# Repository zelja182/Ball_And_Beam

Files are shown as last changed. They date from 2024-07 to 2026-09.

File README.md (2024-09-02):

Sistem za balansiranje lopte na šini

Ovaj projekat se bavi problemom balansiranja lopte na šini i za potrebe istog je uređeno sledeće:
- Isporjektovan sistem za balansiranje lopte na šini u programu za CAD dizajn
- Svi isporjektovani delovi su izštampani na 3D štampaču
- Određen je matematički model sistema
  - Odeđena je jednačina kretanja lopte po šini
  - Određen matematički model hobi servo motora uz pomoć metoda za identifikaciju sistema, odnosno to pokriva
    - Projektovanje platforme za ispitivanje u programu za CAD modeliranje
    - Pokretanje ekspirimenata, prikupljnje i obradu podataka
    - Grey box metod identifikacije sistema - gde je na osnovu poznatih informacija formirana prenosna funkcija, a zatim vrednosti parametra te prenosne funkcije na osnovu prikupljenih i obrađeninih podataka i funkcijom minimizacije estimirani
    - Black box metod identifikacije sistema - cilj ovog dela jeste određivanje matematičkog modela uz pomoć neuronskih mreža i atoregresivnog modela. Preuzeto iz rada https://www.sciencedirect.com/science/article/pii/S2405896320317353
- Konstruisanje i implementacija upravljačkog sistema  --> in progress
- Upoređivanje rezultata simuliranog i stvarnog sistema  --> in progress

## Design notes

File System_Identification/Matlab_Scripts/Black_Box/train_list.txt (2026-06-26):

../../Data/Encoder_data/Test_2/Test_30/Processed/Test_1.csv
../../Data/Encoder_data/Test_2/Test_30/Processed/Test_2.csv
../../Data/Encoder_data/Test_2/Test_30/Processed/Test_4.csv
../../Data/Encoder_data/Test_2/Test_30/Processed/Test_5.csv
../../Data/Encoder_data/Test_2/Test_30/Processed/Test_6.csv
../../Data/Encoder_data/Test_2/Test_30/Processed/Test_9.csv
../../Data/Encoder_data/Test_2/Test_30/Processed/Test_10.csv
../../Data/Encoder_data/Test_2/Test_30/Processed/Test_11.csv
../../Data/Encoder_data/Test_2/Test_30/Processed/Test_12.csv
../../Data/Encoder_data/Test_2/Test_30/Processed/Test_13.csv
../../Data/Encoder_data/Test_2/Test_30/Processed/Test_14.csv
../../Data/Encoder_data/Test_2/Test_45/Processed/Test_1.csv
../../Data/Encoder_data/Test_2/Test_45/Processed/Test_2.csv
../../Data/Encoder_data/Test_2/Test_45/Processed/Test_3.csv
../../Data/Encoder_data/Test_2/Test_45/Processed/Test_4.csv
../../Data/Encoder_data/Test_2/Test_45/Processed/Test_5.csv
../../Data/Encoder_data/Test_2/Test_45/Processed/Test_7.csv
../../Data/Encoder_data/Test_2/Test_45/Processed/Test_8.csv
../../Data/Encoder_data/Test_2/Test_45/Processed/Test_10.csv
../../Data/Encoder_data/Test_2/Test_45/Processed/Test_12.csv
../../Data/Encoder_data/Test_2/Test_45/Processed/Test_13.csv
../../Data/Encoder_data/Test_2/Test_45/Processed/Test_14.csv

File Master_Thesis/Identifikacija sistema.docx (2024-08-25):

# Identifikacija Sistema

Ovde je cilj da se opise ceo postupak identifikacije sistema

# Black Box vs Grey Box method

Ovde hocu da predstavim kako ova dva modela rade i njihove generalne ideje

# Eksperimentalno odredjivanje prenosne funkcije dc servo motora

Ovde hocu da opisem ceo postupak odredjivanje prenosne funkcije

## Prikupljane i obrada podataka

## Grey Box method i Validacija istog

### Matematicki model servo motora

Ovde hocu da objasnim kako sam nasao generalnu prenosno f-ju servo motora

### Grey box metod i validacija

Ovde hocu da opisem kod koji sam koristio za estimaciju i validaciju prenosne f-je

## Black Box method i validacija istog

### Neuralne mreze kao alat u automatskom upravljanju

Kratak uvod u kojem hocu da spomenem DL i objasnim kako se on koristi u automatskom upravljanju --> Akcenat na identifikaciju sistema

### Black Box method

Ovde hocu da opisem kod koji sam koristo za estimaciju i validaciju prenosne funkcije

Izvori:

- Servo Motor tf identification:
  - https://faculty-web.msoe.edu/meier/ee3720/technotes/dcservo.pdf
- System identification:
  - https://indico.cern.ch/event/11749/contributions/1328397/attachments/57048/82143/control_theory_3.pdf
  - https://www.mathworks.com/help/ident/gs/about-system-identification.html
  - https://underactuated.mit.edu/Spring2022/
  - http://groups.csail.mit.edu/locomotion/russt.html
  - https://www.youtube.com/watch?v=YiJRgKJ0My8
  - https://www.youtube.com/watch?v=Z1QS6FsxrJI

Математички модел система

У уводу овог рада смо објаснили укратко конфигурацију систиама, а онда у поглављу “Пројектовање и израда система” објаснили како смо тај систем испројектовали у софтверу за компјутерски адитивни дизајн и затим уз помоћ 3D штампача израдили испројетоване делов које смо касније склопили.

Већ је познато да се наш систем састоји од лоптице која се креће по шини која је спрегнута са серво мотором преко полуга различитх дужина. Да ће нам

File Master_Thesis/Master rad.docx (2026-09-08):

# Мастер рад

# 1. Увод

Управљање нестабилних система је веома важан задатак у аутоматском управљању, а како се ови системи сматрају веома опасним они се испитују у лабораторијама. Систем за балансирање кугле на шини јесте нестабилан систем и може се поистоветити са реалним проблемима као што су хоризонтална стабилизација авиона током слетања или у средини турбулентног струјања.

Систем за балансирања кугле на шини је веома лак за разумевање и многе технике управљања се могу изучавати на њему, па се због тога често може наћи у лабораторијама инжeњера за аутоматско управљање.

Овај систем се састоји од кугле и шине чији се угао заокретања управља мотором. Циљ оваквог система јесте да се кугла заустави на тачно одређеној позицији. Ако је управљање лоше, кугла ће пасти са шине.

Систем балансирања кугле на шини може се реализовати у две конфигурације.

Прва конфигурација је приказана на слици 1.1. Са слике се види да је греда ослоњена у средини и да се ротира око своје централне осе. Оваква конфигурација поседује две предности. Прва предност је та што је лака за израду, а друга јесте то што јој је математички модел релативно једноставан.

Слика 1.1 – Конфигурација 1

Друга конфигурација је нешто сложенија, а приказана је на слици 1.2. У овој конфигурацији греда има две тачке ослонца. Један крај је непокретан и греда се ротира око његове тачке, док је други крај преко система полуга спојен на мотор. Оваква конфигурација је тежа за израду и има мало сложенији математички модел.

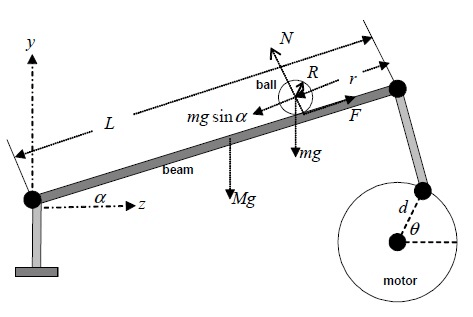
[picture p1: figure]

Слика 1.2 – Конфигурација 2

У овом раду се користи друга конфигурација, упркос сложености. Такође, треба напоменути да су следеће теме обрађене:

- Пројектовање и изрaда система за балансирање кугле на шини,
- Одређивање математичког модела система за балансирање кугле на шини,
- Пројектовање и имплементација регулатора и
- Испитивање у реалном времену.

# 2. Пројектовање и израда система за балансирање кугле на шини

Први проблеми и задаци овог мастер рада јесу пројектовање и израда система за балансирање кугле на шини. А да би се уопште могло испројектовати систем за балансирање кугле на шини потребно је знати одговоре на питања “Шта је циљ овог система? И како уопште он ради?”.

Циљ овог система јесте да доведе куглу на одређену позицију тако што ће сам себе избацити из равнотежног стања. Да би се то боље разумело, претпоставимо да имамо шину дугачку 50cm, да се кугла налази и мирује на десном крају те шине и да је жељена позиција те исте кугле средина шине. У следећем кораку, на основу жељене вредности излаза, мотор треба да заротира излазно вратило за угао α и нагне шину на лево, односно за угао β, сензор очита нову позицију кугле, која сада креће према средини, а затим регулатор на основу разлике жељене и стварне позиције кугле формира нови управљачки сигнал за мотор. У другом кораку мотор ће поново заротирати излазно вратило за угао α и кориговаће угао шине, а сензор очита нову позицију кугле и помоћу регулатора формирати нови сигнал за мотор. Ови кораци ће се понављати све док се кугла не доведе на жељену позицију. Све претходно објашњено може се представити и једним блок дијаграмом који је приказан на слици 2.1.

Слика 2.1 – Уопштени блок дијаграм система за балансирање кугле на шини

На основу блок дијаграма и изабране конфигурације система могу се формирати и додатна потпитања:

- Којим сензором се мери позиција кугле на шини? Којим мотором се гони цео систем? Којим контролером се систем управља?
  - За мерење позиције изабран је ласерски сензор удаљености VL53L0X, за извршни орган серво мотор непознатог произвођача и за формирање и прослеђивање управљачког сигнала микроконтролер Arduino Uno. Техничка документација и више информација о овим компонента, као и осталим компонентама које су коришћене приликом израде овог мастер рада, може се пронаћи на крају овог рада у додатку А.
- Како ће се сви испројектовани, нестандардни, делови израдити?
  - Сви делови који су испројектовани за овај мастер рад су израђени адитивном технологијом израде, тј. на 3D штампачу.

## 2.1. Пројектовање система за балансирање кугле на шини

Након што су дати одговори на сва претходна питања, слика самог система постаје јаснија и може се приступи пројектовању и моделирању система.

Први део који је испројектован јесте шина и она је кроз пар итерација добила следећи облик:

Слика 2.2 – Шина са куглом

Са слике се може видети да се шина састоји од четири дела: две половине шине и два граничника. Половине шине су међусобно спојене вијчаном везом на средини, док су граничници причвршћени епоксидним лепком на њеним крајевима.

Једна половина шине поседује ушицу која служи за спајање са ослонцем. На њеном крају налази се и граничник са ушицом, преко које се шина, посредством система полуга, повезује са мотором. Други граничник уједно представља носач ласерског сензора удаљености.

Следећи испројектовани део јесте носач шине. Носач се састоји из три дела; ушице, навојне шипке и базе. Делови су спојени навијањем на навојну шипку. На једном крају шипке навијена је ушица, а на другом база. Цео носач је затим зашрафљен за постоље од иверице.

Слика 2.3 – Шина са носачем

Након шине и носача, било је потребно испројектовати и додати везу између шине и мотора, сензор, микроконтролер и носаче за микроконтролер и серво мотор. Веза између шине и мотора се састоји из две полуге различитих дужина, где је дужа полуга повезана са шином на једном крају, а на другом крају са мањом полугом, која је повезана са серво мотором.

Финални модел система за балансирање кугле на шини приказан је на слици 2.4

Цео овај систем је измоделиран у софтверу за Компјутерски Адитивни Дизајн (CAD) CATIA и може се пронаћи на следећем линку:

https://github.com/zelja182/Ball_And_Beam/tree/main/Ball_and_Beam_CAD_model

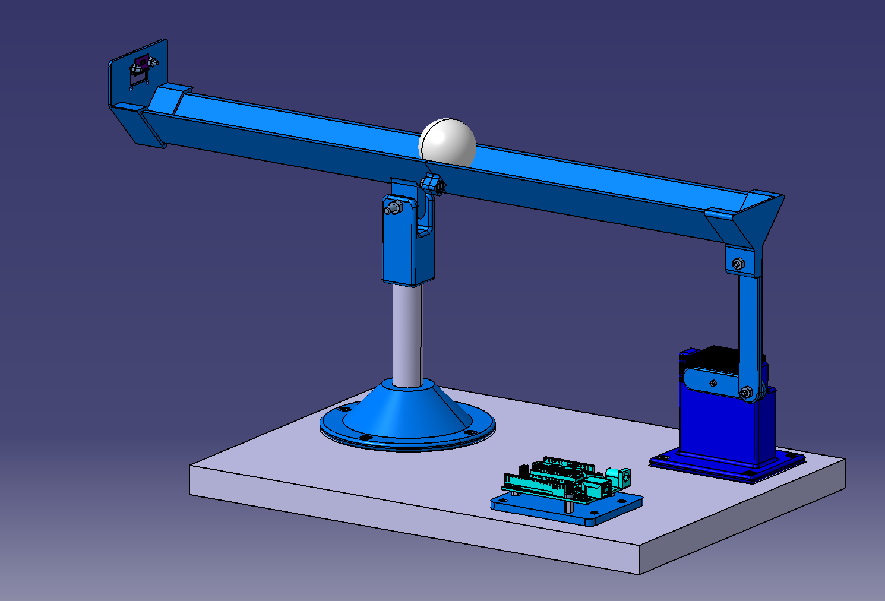
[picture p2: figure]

Слика 2.4 – Систем за балансирање кугле на шини

## 2.2. Израда пројектованих делова

Адитивна производња, позната и као 3D штампа или адитивна израда, је процес израде тродимензионалних објеката додавањем материјала у слојевима, уместо сечења или обликовања материјала.

У адитивној производњи, машине користе податке о CAD моделу да би додавале материјал у слојевима да би се израдио објекат, за разлику од традиционалних начина производње где машине уклањају материјал из блока или компоненте да би се добио жељени део.

Адитивна производња, у даљем тексту 3D штампа, има многе предности у односу на традиционалну производњу, укључујући већу сложеност дизајна, брзину производње, ниског трошкова производње малих серија или јединичних производа, могућност производње на захтев и низ других предности.

Због свих ових предности 3D штампач је нашао велику примену у различитим индустријама као што су авио и аутомобилска, медицинска и многе друге индустрије, али поред индустрије 3D штампач је постао и стандардна опрема многих лабараторија, као и радионица разних хобиста.

Постоје различите врсте 3D штампања, а неке од њих јесу фузија ласера, слој по слој (FDM) и селективна ласерска синтеризација (SLS). Која ће се врста 3D штампе користити зависи од жељеног материјала, величине објекта и других фактора.

За потребе мастер рада, сви пројектовани, нестандардни, делови израђен су на 3D штампачу Ender 3 Pro (слика 2.5) компаније Creality. Овај штампач користи технологију слој по слој (FDM), а његове основне карактеристике могу се видети у табели 2.1.

Слика 2.5 – Ender 3 Pro

Назив штампача | Ender 3 Pro
Запремина штампања | 220x220x250mm
Габарити штампача | 440x410x465mm
Пречник млазнице | 0.4mm
Максимална температура млазнице | 250°C
Максимална температура подлоге за штампање | 110°C
Висина слоја | 0,1–0,4mm
Повезвање | USB, SD картица
Материјали за штампање | PLA, ABS, PETG, TPU

Техничке карактеристике штампача Ender 3 Pro – Табела 2.1

Припрема делова за штампу је урађена у софтверу UltiMaker Cura. Сви делови су израђени од PLA пластике и са истом прецизношћу и за ту потребу температура подлоге за штампу је подешена на 55°C, температура млазнице на 215° и висина слоја на 0,2mm. Параметри попут дебљине зида, типа и густине испуне разликују се од дела до дела.

За израду свих делова, узимајући у обзир и шкартове, било је потребно 96 сати. Систем је склопљен следећим редом:

1. Састављање носача шине
2. Састављање шине и монтирање сензора на исту
3. Позиционирање и фиксирање носача шине и носача серво мотора
4. Спајање шине и носача шине
5. Монтирање серво мотора на носач истог
6. Спајање шине и серво мотора полугом
7. Позиционирање и фиксирање носача за микро контролер
8. Монтирање микроконтролера на носач за исти
9. Ожичавање система пратећи шему са слике 2.6

Слика 2.6 – Шема повезивања система за балансирање кугле на шини

# 3. Математички модел система за балансирање кугле на шини

Аутоматско управљање је мултидисциплинарна грана инжењерства усмерена на пројектовање, анализу и имплементацију система који контролишу понашање динамичких процеса. Главни задаци ове гране јесу идентификација система, која обухвата моделирање система, процену параметара и валидацију модела, и управљање системом, чији је циљ да систем учини стабилнијим, одзивнијим и прецизнијим.

На основу претходно реченог лако је закључити да су наредна два корака идентификација система и пројектовање алгоритма за управљање. С обзиром да је познавање математичког модела система предуслов за пројектовање алгоритма за управљање, онда је и јасно да ће у овом поглављу главни циљ бити идентификација самог система, односно одређивање његовог математичког модела.

Дефиниција 1 Модел физичког система је идеализовани, замишљени, систем који задржава особине стварног система битне за његову анализу.

Дефиниција 2 Математички модел система је формални математички опис модела физичког система који успоставља једнозначну везу између излазних и улазних величина за произвољне промене улазних величина и за произвољне почетне услове, а исказан је помоћу математичких симбола, операција и релација.

Ако се претпостави да математички модел довољно тачно описује физички систем, тј. модел физичког система, и да представља његов веродостојан опис, онда он садржи све информације о физичким особинама система. Тада се проучавање тог физичког система могу извршити на његовом математичком моделу.

У колико су динамика система и његови параметри познати, до математичког модела система може се доћи користећи законе физике. Претпоставимо да је систем представљен на следећој слици:

Слика 3.1 – Систем пригушеног осцилаторног кретања тела

и да су познати сви параметри овог система C, k и m. Користећи знање Механике може се закључити да овај систем преставља пригушено осцилаторно кретање тела и да се он може описати следећом једначином:

m (d^2 y)/(dt^2)+c (dy)/(dt)+ky(t)= F(t) (3.1)

Претходна једначина јесте математички модел система са слике која се даље може користити за анализу система. Овакав систем се у жаргону назва белом кутијом, јер су сви његови параметри познати, као и његова динамика.

Супротно од беле кутије, јесте црна кутија, односно модели чија динамика је непозната. У оваквим случајевима идентификација система, као засебна област аутоматског управљања, долази до изражаја.

Приликом одређивања математичког модела система непознате динамике, први корак јесте прикупљање информација о систему. Овај корак подразумева извођење експеримената над системом и то тако што се систем побуђује одређеним улазним величинама, а сам излаз система мери.

Следећи корак би био одабир структуре модела. За структуру система може се одабрати преносна функција са n-тим бројем полова и m-тим бројем нула, диференцијална једначина, ауто-регресивни модел, неуронска мрежа или било који други модел.

Након што су прикупљене информације о систему и одабрана структура модела, потребно је естимирати параметре и валидирати модел. Приликом валидације система треба користити нов сет података, где ће се улази тог сета искористити за побуду модела, а затим излази модела и стварног система поредити.

Када се све сумира, идентификација система се састоји од експеримента и прикупљање улазно-излазних података система, одабира структуре модела, естимације параметара и валидацију модела; али “Како изабрати праву структуру система?” и “Шта радити ако након валидације критеријуми нису задовољени?”. Ствар јесте у томе што правила приликом одабира структуре модела нема и ако након валидације модела критеријуми нису задовољени, потребно је вратити се на “почетак” и изабрати нову структуру или модификовати претходно изабрану, а затим поново естимирати параметара и валидирати модел. Идентификација система јесте процес који захтева више итерација да би се постигли жељени резултати, али и процес у којем искуство може бити од великог значаја.

Дефиниција 3 Идентификација система је методологија за конструисање математичког модела динамичког система користећи мерене улазне и излазне сигнале система.

Процес идентификације система састоји се из:

- Мерење улазних и излазних сигнала система у временском или фреквентном домену,
- Одабира структуре система,
- Естимације параметара за изабрану структуру модела и
- Валидације самог модела.

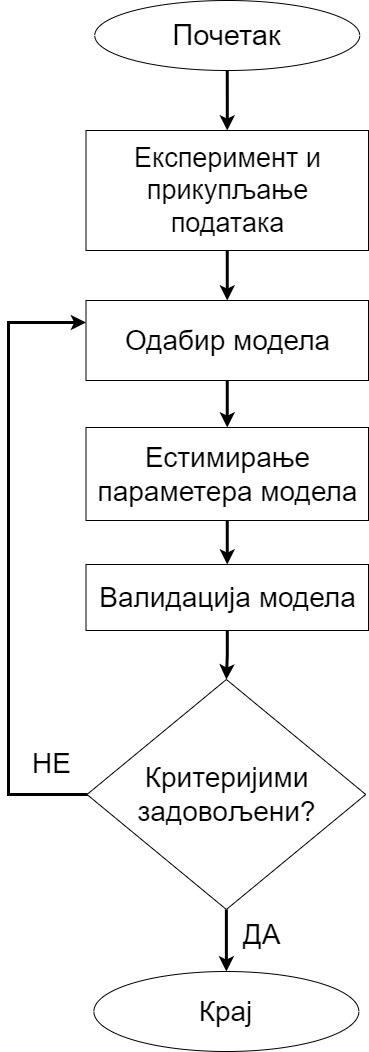
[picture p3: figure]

Слика 3.2 – Алгоритам за идентификацију система

Поред, такозваних, белих и црних кутија, постоје и сиве кутије. То су системи чија је динамика добрим делом позната, али не и параметри, или барем не сви. У оваквим случајевима се користи, претходно објашњена, метода за идентификацију система.

Претпоставимо поново да је задатак одређивање математичког модела система приказаног на слици 3.1, при чему је једини познати параметар маса тела. Пратећи алгоритам за идентификацију система, први корак јесте прикупљање информација о систему. Након тога потребно је одабрати структуру модела. Уколико се на основу познатих динамичких карактеристика система претпостави да се његово понашање може описати моделом масе, опруге и пригушивача, као структура модела може се одабрати једначина (3.1). Затим би се применом неке од метода минимизације естимирали непознати коефицијенти c и k, а на крају би се, коришћењем новог скупа улазно-излазних података, извршила валидација модела.

За валидирање модела често се упоређују стварни одзив и одзив модела, али се за боље разумевање самог система користи и анализа резидуала.

Дефиниција 6 Анализа резидуала је статистичка техника која се користи у идентификацији система како би се проценила тачност и квалитет модела анализом разлике између стварног излаза система и излаза предвиђеног моделом (3.2.29).

r(t)=y_(измерено) (t)-y_(предвиђено) (t) (3.2)

Ове разлике, познате као резидуи, представљају необјашњени део излаза који модел не хвата. Анализа резидуа помаже да се утврди да ли модел добро захвата основну динамику система или има систематске грешке.

Дефиниција 7 Аутокорелација резидуала се односи на корелацију резидуа са самим собом на различитим временским интервалима. Ако постоји значајна аутокорелација, то сугерише да модел не хвата у потпуности понашање система.

Дефиниција 8 Унакрсна корелација резидуала проверава да ли су резидуи у корелацији са прошлим улазима. Ако су резидуи у корелацији са улазом, то сугерише да модел не успева да ухвати неку важну динамику система под утицајем улаза.

Посматрајући систем за балансирање лопте на шини се састоји од лопте на шини која је системом полуга спојена на серво мотор, где је серво мотор извршни орган, а лопта на шини објекат система. Математички модел објекта може се извести користећи законе кинематике и динамике, док је математички модел извршног органа, узимајући у обзир да ова информација није дата у техничког документацији, потребно наћи користећи један од метода за идентификацију система.

## 3.1. Једначина кретања кугле на шини

Тумачећи конфигурацију система са слике 1.2 може се доћи до закључка да брзина и смер кретања лопте на шини зависи од промене нагибног угла шине, односно промене угла излазног вратила серво мотора.

### 3.1.1. Једначина промене нагибног угла шине

Једначина промене нагибног угла шине може се наћи решавањем проблема приказаног на слици 3.3, где су:

- l1 – дужина краће полуге,
- l2 – дужина дуже полуге,
- L – растојање између ослонца шине и гоњеног краја шине,
- α – нагибни угао шине,
- ωα – угаона брзина шине,
- θ – угао излазног вратила серво мотора и
- ωθ – угаона брзина серво мотора.

Слика 3.3 – Систем полуга система за балансирање лопте на шини –

Брзине VA и VB су представљене у следећем облику:

V_A = ω_θ l_1 , (3.1.1)

V_B = ω_α L. (3.1.2)

Користећи теорију сличности троуглова може се закључити следеће:

V_B = V_A cosθ. (3.1.3)

Комбиновањем једначина (3.1.1), (3.1.2) и (3.1.3) добија се:

ω_α L = ω_θ l_1 cosθ. (3.1.4)

и ако се настави са даљим разлагањем претходне једначине, може се доћи до следеће једначине:

(dα)/(dt) = (l_1)/L(dθ)/(dt)cosθ. (3.1.5)

Интеграљењем једначе (3.1.5) довија се:

α= (l_1)/Lsinθ+C. (3.1.6)

Ако важе следеће претпоставке:

sinθ≈θ за веома мале вредности угла θ и (3.1.7)

α_0 =0 → C=0. (3.1.8)

Онда из (3.1.8) и (3.1.9) следи једначина промене нагибног угла шине у зависности од промене угла вратила на серво мотору:

α= (l_1)/Lθ. (3.1.9)

### 3.1.2. Једначине кретања кугле на шини и преносна функција објекта

За потребе налажења једначине кретање лопте на шини потребно је посматрати случај када је нагибни угао шине различит од нуле (α≠0). Узимајући претходну претпоставку у обзир, проблем се може поистоветити са проблемом кретање лопте по стрмој равни (слика 3.4).

Слика 3. 4 – Кретање лопте по стрмој равни

За решавање овог проблема потребно је кренути од једначине суме свих сила на тело:

F=mg+N+F_(tr) . (3.1.10)

Узимајући у обзир да се за овај пројекат користи кугла са веома малом масо, може се занемарити сила потиска, а са њом и сила трења. Стога једначина (3.1.11), пројектована на x осу, имати следећи облик:

F(t)=mg sinα(t), (3.1.11)

односно, ту исту једначина може се записати и у следећем облику:

(I/(R^2)+m)x(t)= -mg sinα(t) . (3.1.12)

Где су:

- I – момент инерције лопте,
- R – полупречник лопте,
- m – маса лопте,
- x(t) – убрзање лопте,
- g – гравитационо убрзање,
- α – нагибни угао шине.

Ако претпоставимо да је:

sinα≈α за веома мале вредности угла α, (3.1.13)

тада једначину (3.1.12) можемо написати у следећем облику:

(I/(R^2)+m)x(t)= -mg α(t). (3.1.14)

Односно, када се угао α замени његовом релацијом из једначине (3.1.10), тада се добија:

(I/(R^2)+m)x(t)= -mg (l_1)/Lθ(t), (3.1.15)

односно:

x(t)= -(mgl_1)/(L(I/(R^2)+m))θ(t) . (3.1.16)

До преносне функције објекта долази се пребацивањем једначине (3.1.14) из временског домена у комплексни уз помоћ Лапласове трансформације:

s^2 x(s)= -(mgl_1)/(L(I/(R^2)+m))θ(s) . (3.1.17)

Након сређивања једначине (3.1.15) добија се следећа преносна функција:

W_O (s)=(x(s))/(θ(s))= -(mgl_1)/(L(I/(R^2) + m)) 1/(s^2), (3.1.18)

која након замене симбола њиховим вредностима, добијамо облик:

W_O (s)= -0.80541872/(s^2). (3.1.19)

## 3.2. Математички модел серво мотора једносмерне струје

Одређивању математичког модела серво мотора приступљено је на два начина. Први начин јесте идентификација методом сиве кутије, где је на основу општих познатих информација о серво мотору формирана структура модела. Други начин јесте идентификација методом црне кутије. Пратећи алгоритам за идентификацију система, у овом поглављу обрађени су следећи кораци:

- прикупљање података помоћу експеримента,
- избор структуре модела,
- естимација параметара модела и
- валидација модела.

### 3.2.1. Прикупљање података помоћу експеримента

#### 3.2.1.1. Пројектовање и израда платформе за испитивање

За потребе експеримента било је потребно конструисати платформу за испитивање. До решења се дошло одговорима на следећа питања:

- Шта је циљ експеримената?
  - Циљ експеримента јесте прикупљање улазних и излазних величина система.
- Шта је улазни величина серво мотора, а шта излазна?
  - За улазну величину серво мотора је изабран жељени угао излазног вратила мотора, који је уз помоћ једноставне формуле трансформисан у ширинско модулисани пулс (стварна улазна величина), док је излаз мотора промена угла излазног вратила серво мотора.
- Како и чиме мерити промену излазне величине серво мотора?
  - Промена излазне величине серво мотора, односно промена угла излазног вратила серво мотора, мерена је ротационим енкодером LPD3806. Нешто више о овом енкодеру може се пронаћи у додатку А на крају овог рада.

Водећи се одговорима на претходна питања испројектована и израђена је платформа за испитивање која је поседује дрвено постоље, за које су вијцима причвршћени носачи серво мотора и ротационог енкодера. Вратила мотора и ротационог енкодера спрегнута наменски пројектованом спојницом. Оба носача и спојница су израђени на 3D штампачу, а финални производ је приказан на слици 3.5.

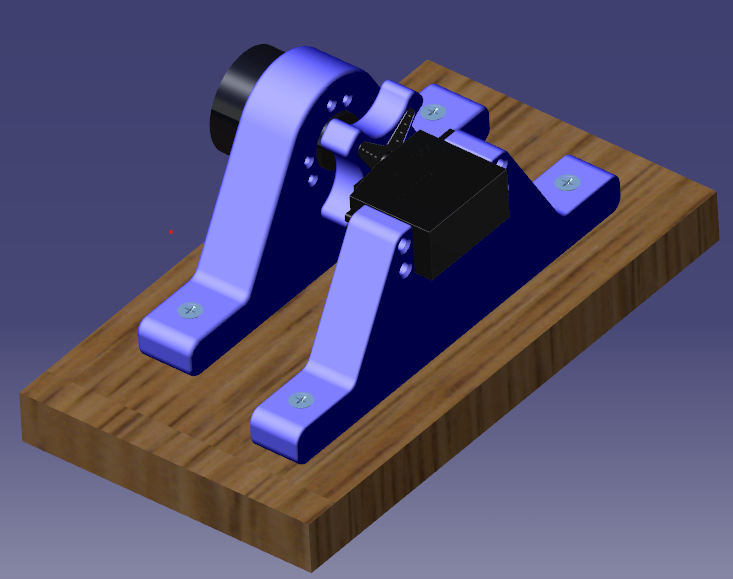
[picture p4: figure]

Слика 3.5 – Платформа за испитивање серво мотора

#### 3.2.1.2. Поставка експеримента и прикупљање података

У претходном делу је споменуто да је главни циљ овог експеримента прикупљање улазних и излазних величина серво мотора које ће се касније искористити за естимацију параметара модела. На основу циља може се закључити да експеримент треба да садржи следеће кораке:

- побуду серво мотора одређеном улазном величином,
- очитавање промене излазне величине и
- чување податка о променама улазних и излазних величина.

На први поглед задатак делује једноставан, међутим финално решење дошло се тек у трећој итерацији.

Итерација 1

У првој итерацији, идеја је била да се и за побуду серво мотора и за очитавање промене угла излазног вратила серво мотора помоћу ротационог енкодера, користи један микроконтролер (Arduino Uno). У главној петљи се налазио код који је слао одређени ширински модулисани пулс серво мотору, док се у прекидној петљи налазио код који би очитавао вредности са енкодера.

Главна петља ради непрекидно, извршавајући редовне задатке у секвенцијалном редоследу. Насупрот томе, прекидна петља се активира одређеним догађајима, омогућавајући контролеру да привремено заустави главну петљу и брзо одговори на хитне, временски осетљиве задатке пре него што се врати у главну петљу.

На основу претходно објашњене идеје и објашњене разлике између главне и прекидне петље, може се закључити да је систем често улазио у прекидну петљу, а да су последице тога испрекидан ширинско модулисани пулс који је слат мотору, као и јако вибрирање мотора.

Слика 3.6 – Шема за повезивања у првој итерацији

Итерација 2

На основу искуства из прве итерације, у другој итерацији решено је да се користе два микроконтролера (Arduino Uno). Један је служио за побуђивање серво мотора, а други за очитавање ротационог енкодера. Поред ротационог енкодера и серво мотора, оба микроконтролера су поседовала по тастер и лед диоду (шеме повезивања приказана је на слици 3.7)

Лед диода на контролеру, који је служио за покретање серво мотора, је светлела све до притиска тастера. Након притиска тастера, лед диода би се угасила, затим би био извршен експеримент, где мотор ротира излазно вратило за одређени угао и након кратке паузе га враћа у почетни положај. Након извршеног експеримента лед диода би поново засијала.

Сличан алгоритам је био и на другом микроконтролеру, али је битно напоменути да је део алгоритма за очитавање и чување вредности са енкодера и даље био у прекидној петљи. Што се тиче алгоритма у главној петљи, након притиска тастера диода би засијала, затим би се сви прикупљени подаци слали преко серијског порта на рачунар и након завршеног слања, диода би се угасила сигнализирајући да су сви подаци послати и да је други контролер спреман за нови експеримент.

У овој итерацији пронађена су два проблема. Један од проблема јесте био нестабилан рад серво мотора услед нестабилног напајања. Други проблем је био слање прикупљених података. Због количине прикупљених података на самом почетку слања података микроконтролер би се сам од себе ресетовао.

Слика 3.7 – Шема повезивања у другој итерацији

Итерација 3

У трећој итерацији, микроконтролер (Arduino Uno) који смо користили за очитавање вредности са енкодера је замењен микропроцесором (Raspberry Pi) и проблем са напајањем серво мотора је решен. Алгоритми за покретање серво мотора и очитавање вредности са ротационог енкодера добрим делом остали исти. У наставку су приложене шема за повезивање (слика 3.8), као и скрипте за прикупљање података и покретање серво мотора.

Слика 3.8 – Шема повезивања у трећој итерацији

Као што је напоменуто, за мерење промене угла излазног вратила серво мотора употребљен је ротациони енкодер који је повезан на микропроцесор Raspberry Pi. Поред енкодера на овај контролер повезани су тастер и лед диода. Лед диода је индикатор која светли када је у току чување података који се чували након што се експеримент заврши и притисне тастер у датотеку json формата. Цео алгоритам је приказан на слици 3.9.

Скрипта за ове намене писана је у програмском језику Python и искоришћене су следеће библиотеке:

- pigpio – библиотека која омогућава коришћење и управљање улазно-излазних пиновима генералне намене микропроцесоре Raspberry Pi,
- time – библиотека за очитавање времена,
- json – библиотека за рад са подацима и датотекама у json формату и
- rotary_encoder – библиотека која омогућава очитавање вредности са ротационог енкодера.

Треба напоменути да је скрипта сачињена и од следећих функција:

- callback – функција прекидне петље која очитава вредност ротационог енкодера и повећава, односно смањује, бројач,
- collect_data – функција која је у директној вези са callback функцијом и служи за смештање очитаних података у привремене низове,
- save_data – функција за чување очитаних података у датотеку json формата,
- var_reset – функција која служи за ресетовање и брисање свих бројача и низова које користимо за привремено смештање очитаних вредности,
- debounce – функција која служи за решавање проблема са поскакивањем сигнала тастера,
- button_press_handler – ова функција се можда може и назвати главном функцијом главне петље, јер она у себи садржи наредбе и функције за паљење и гашење лед диоде, чување очитаних података и ресетовање привремених податка, а притом је у директној спрези са debounce функцијом.

Проблем са поскакивањем сигнала (енг. bouncing signal problem) је карактеристичан проблем за електро механичке компоненте попут тастера.

Приликом притиска тастера два метална дела долазе у контакт како би затворили електрично коло. У идеалном случају, та два дела се спајају у једном тренутку (у трену), док у стварности та два дела долазе у контакт неколико пута пре коначног спајања. Ово узрокује вишеструка окидања која контролер поистовећује са вишеструким притиском тастера. Овај ефекат се дешава и приликом отпуштања тастера.

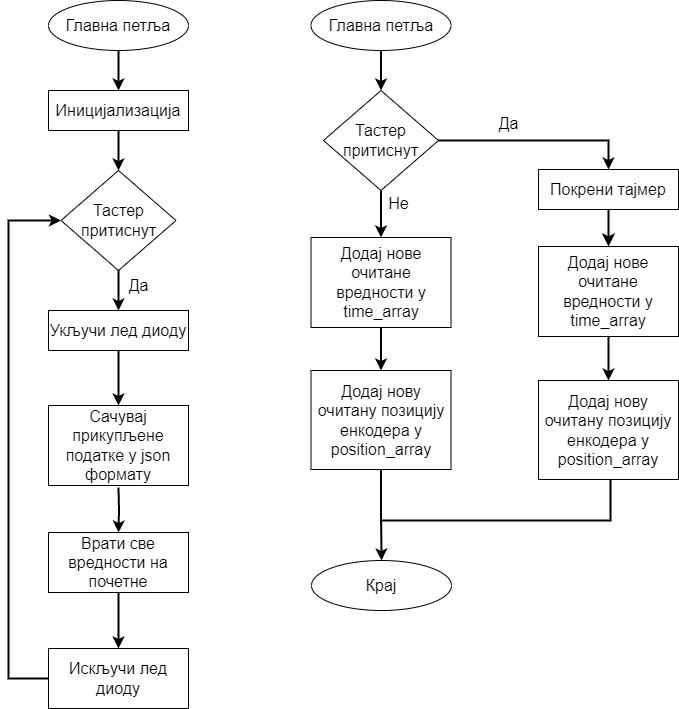
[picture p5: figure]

Слика 3.9 – Алгоритам за очитавање промене угла излазног вратила серво мотора и чување очитаних података

import pigpio

import time as t

import json

from Scripts import rotary_encoder

BUTTON_PIN = 23 # GPIO PIN

LED_PIN = 14 # GPIO PIN

channel_A = 20 # GPIO PIN

channel_B = 21 # GPIO PIN

position = 0

position_array = []

time_array = []

time_start = 0

test_count = 0

def save_data():

global test_count

path = "/Master Rad/Test_data/Test_"

data = {

"Counts": position_array,

"Time": time_array,

}

with open(path + str(test_count) + ".json", "w") as f:

json.dump(data, f)

test_count += 1

def var_reset():

global position, position_array, time_array

position = 0

position_array = []

time_array = []

def collect_data():

global time_start

if not position_array:

time_start = t.monotonic_ns()

time_array.append(0)

position_array.append(position)

else:

time_array.append(t.monotonic_ns() - time_start)

position_array.append(position)

def callback(way):

global position

position += way

collect_data()

def debounce(func, wait_time=0.01):

last_time = 0

def debounced_func(*args, **kwargs):

nonlocal last_time

current_time = t.time()

if current_time - last_time >= wait_time:

last_time = current_time

return func(*args, **kwargs)

return debounced_func

pi = pigpio.pi()

decoder = rotary_encoder.decoder(pi, channel_A, channel_B, callback)

pi.set_mode(BUTTON_PIN, pigpio.INPUT)

pi.set_pull_up_down(BUTTON_PIN, pigpio.PUD_UP)

pi.set_mode(LED_PIN, pigpio.OUTPUT)

@debounce

def button_press_handler():

pi.write(LED_PIN, 1)

t.sleep(1)

print(max(position_array))

save_data()

var_reset()

pi.write(LED_PIN, 0)

try:

while True:

if not pi.read(BUTTON_PIN):

button_press_handler()

t.sleep(0.01) # Small sleep to avoid busy-waiting

except KeyboardInterrupt:

print("Exiting...")

finally:

decoder.cancel()

pi.stop()

На микроконтролер Arduino Uno повезани су мотор, лед диода и тастер. Лед диода сија све док се не притисне тастер који ту исту диоду гаси и прелази на извршавање експеримент из одређене групе, односно покретање test функције. Скрипта за Arduino Uno је писана у програмском језику C у наменском развојном окружењу за овај контролер (Arduino IDE). За писање ове скрипте поред стандардних функција које нуди стандардна Arduino.h библиотека, коришћене су и библиотека која нам омогућава лако управљање серво мотора (Servo.h), као и Time.h библиотека. Скрипта се састоји од следећих функција:

- setup – ова функција је задужена за иницијализацију пинова,
- loop – је функција главне петље која би гасила лед диоду приликом притиска на тастер и затим покретала један од тестова,
- test_1 – функција за прву групу експеримената и,
- test_2 – функција за другу групу експеримената.

Алгоритам функције test_1 приказан је на слици 3.10 (лево). Скуп углова који су коришћени за овај експеримент јесте α ϵ (-45°, -30°, -20°, -10°, 10°, 20° 30°, 45°, 60°). Обзиром да је за потребе овог мастер рада изабран хоби серво мотор, који има позициону толерирају од ±3°, експеримент је поновљен пет пута за сваки угао α.

Функција test_2 је мало сложенија од претходне функције. Ова функција је давала шест насумичних сигнала (углова) са насумично одређеним паузама. Након шестог сигнала, контролер би послао седми сигнал, који је за циљ имао да врати излазно вратило серво мотора у почетни положај. Користећи функцију test_3 изведено је по петнаест експеримената за две различите конфигурације.

- Конфигурација 1
  - опсег насумичних углова – од -45° до 45°,
  - θ0 = 0°,
- Конфигурација 2
  - опсег насумичних углова – од -30° до 30°,
  - θ0 = 0°.

Алгоритам ове функције је приказан на слици 3.10 (десно).

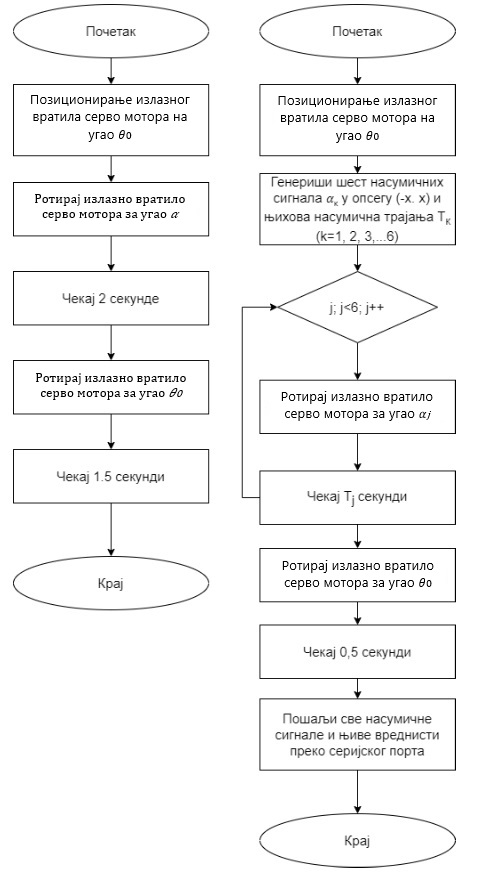
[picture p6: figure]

Слика 3.10 – Алгоритми за извршавање експеримената; алгоритам лево – test_1; алгоритам десно – test_3

#include <Servo.h>

#include "Timer.h"

int test_angles[8] = {-45, -30, -20, -10, 10, 20, 30, 45};

int zero_pwm = map(0, -135, 135, 500, 2500);

unsigned int time_var = 0;

int i=0;

int j=0;

Servo my_servo;

Timer my_timer(MICROS);

void test_1()

{

if(i==8)

{

Serial.println("The end of test");

i++;

}

else if (i<8)

{

int angle;

int pwm = map(test_angles[i], -135, 135, 500, 2500);

Serial.print("Test_1 no. ");

Serial.print(i+1);

Serial.print(".");

Serial.print(j);

Serial.println(" ");

// Print Test Angle

Serial.print("Test angle: ");

Serial.println(test_angles[i]);

Serial.print("Test pwm: ");

Serial.println(pwm);

// Execute Test

my_timer.start();

my_servo.writeMicroseconds(pwm);

delay(2000);

time_var = my_timer.read();

my_servo.writeMicroseconds(zero_pwm);

delay(1500);

// Print Execution Time

Serial.print("Execution time: ");

Serial.println(time_var);

my_timer.stop();

// Handle Counters

j++;

if(j>=5)

{

i++;

j = 0;

}

}

}

void test_2()

{

if(i==15)

{

Serial.println("The end of test");

i++;

}

else if (i<15)

{

int random_angles[6];

int random_pwms[6];

int random_delay[6];

// Generate data for test

for(j=0;j<6;j++)

{

random_angles[j] = random(-45, 45); // Test data 2-1

// random_angles[j] = random(-30, 30); // Test data 2-2

random_pwms[j] = map(random_angles[j], -135, 135, 500, 2500);

random_delay[j] = random(10, 100) * 10;

}

// Execute Test

my_timer.start();

for(j=0;j<6;j++)

{

my_servo.writeMicroseconds(random_pwms[j]);

delay(random_delay[j]);

}

my_servo.writeMicroseconds(zero_pwm);

delay(500);

time_var = my_timer.read();

Serial.print("Test_2 no. ");

Serial.print(i+1);

Serial.println(" ");

// Print Execution Time, Angles and Delays

for(j=0;j<6;j++)

{

Serial.print("angle");

Serial.print(": ");

Serial.println(random_angles[j]);

Serial.print("delay");

Serial.print(": ");

Serial.println(random_delay[j]);

}

Serial.print("Execution_time: ");

Serial.println(time_var);

my_timer.stop();

// Handle Counters

i++;

}

}

void setup() {

// put your setup code here, to run once:

Serial.begin(115200);

pinMode(2, INPUT_PULLUP); // Button Pin

pinMode(7, OUTPUT); // LED Pin

my_servo.attach(5); // Servo Pin

my_servo.writeMicroseconds(zero_pwm);

Serial.print("Zero pwm: ");

Serial.println(zero_pwm);

}

void loop() {

if(digitalRead(2))

{

digitalWrite(7, HIGH);

}

else

{

delay(1500);

digitalWrite(7, LOW);

test_2();

}

}

#### 3.2.1.3. Обрада података

Након прикупљања података било је потребе за обрадом истих. Сви прикупљени подаци су у json формату и садрже два низа. Један низ садржи позиције у датим тренуцима, а други низ садржи временске тренутке очитаних позиција у нано секундама.

Добар део обраде података је аутоматизован скрипта написаних у Python програмском језику. Скрипта Data_processing_1.py је аутоматизовала обраду податка прикупљене експеримента који су покренути функцијом test_1. Позиције које су дате сумом очитаних пулсева ротационог енкодера су претворене у углове, време је из нано секунди претворено у секунде и додате су и вредности улазних сигнала. Узимајући у обзир:

- паузу од две секунде, која је карактеристична за прву и другу групу експеримената,
- да је излазно вратило серво мотора стизало до жељеног угла пре него што две секунде истекну и
- да су бележене само промене угла излазног вратила серво мотора.

Било је лако закључити да датотеке, у којима су сачуване мерене вредности, не садрже податке од тренутка када вратило достиже жељену позицију до почетног тренутка када се вратило враћа у почетни положај. Овај проблем је такође решен уз помоћ скрипте.

Након сређивања података помоћу скрипте, сви сетови података су прегледани и по потреби ручно исправљени.

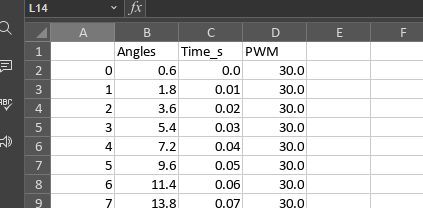
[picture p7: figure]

Слика 3.11 – Подаци након сређивања

Претходно објашњен процес је примењен и на податке прикупљене извршавањем трећег експеримента (test_3). За потребе сређивање ових података коришћене су скрипта Data_processing_2.py.

Сви обрађени подаци су графички приказани на сликама у наставку.

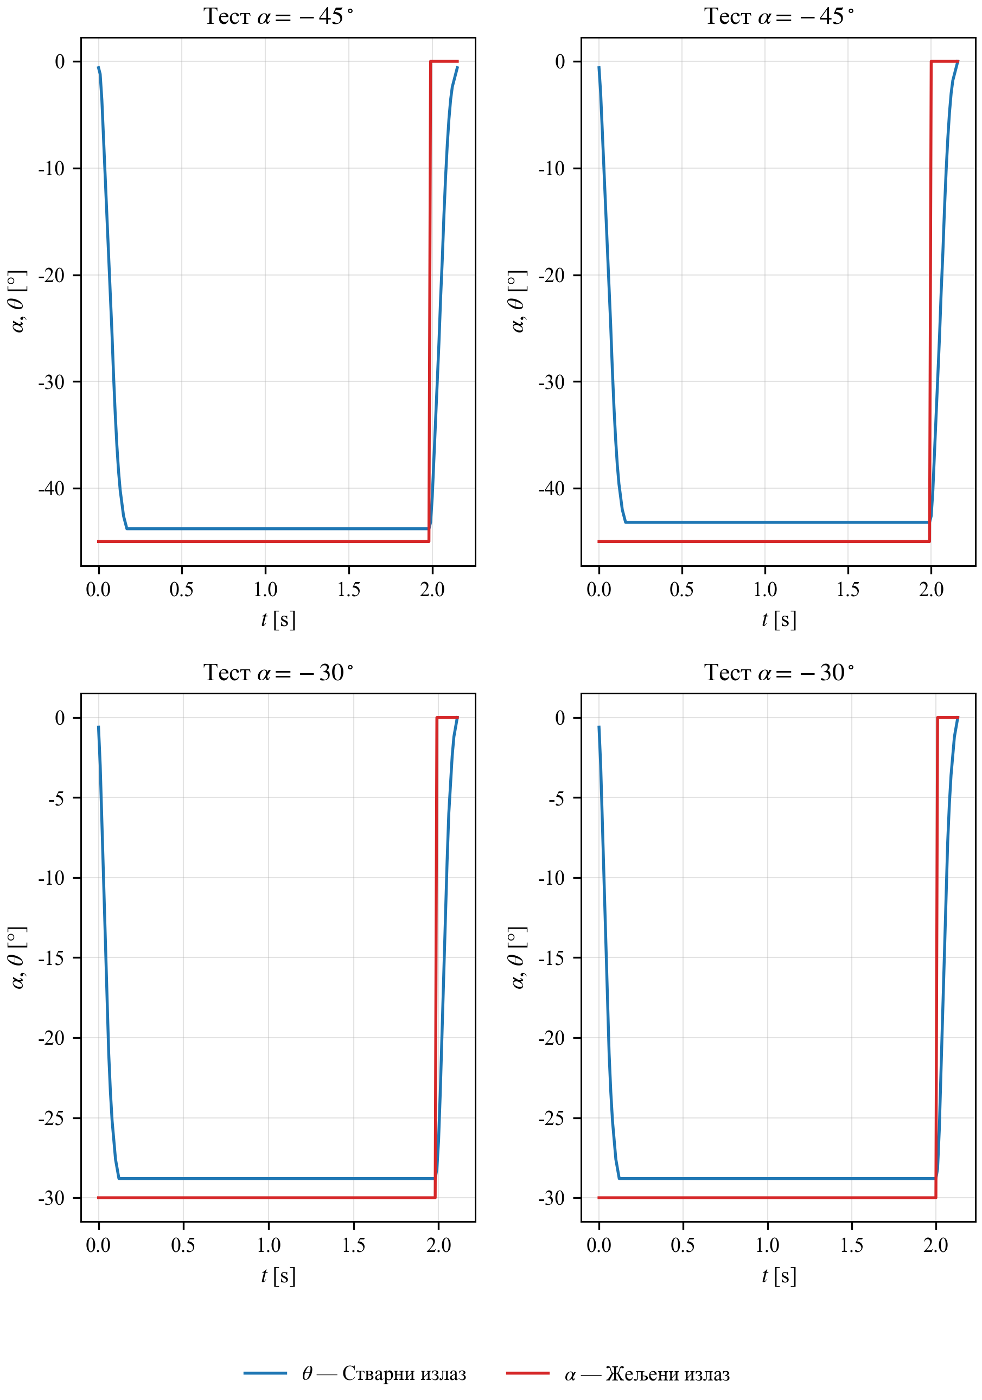
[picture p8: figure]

Слика 3.12а – Графички приказ података прикупљених експериментом 1

Слика 3.12б – Графички приказ података прикупљених експериментом 1

Слика 3.12в – Графички приказ података прикупљених експериментом 1

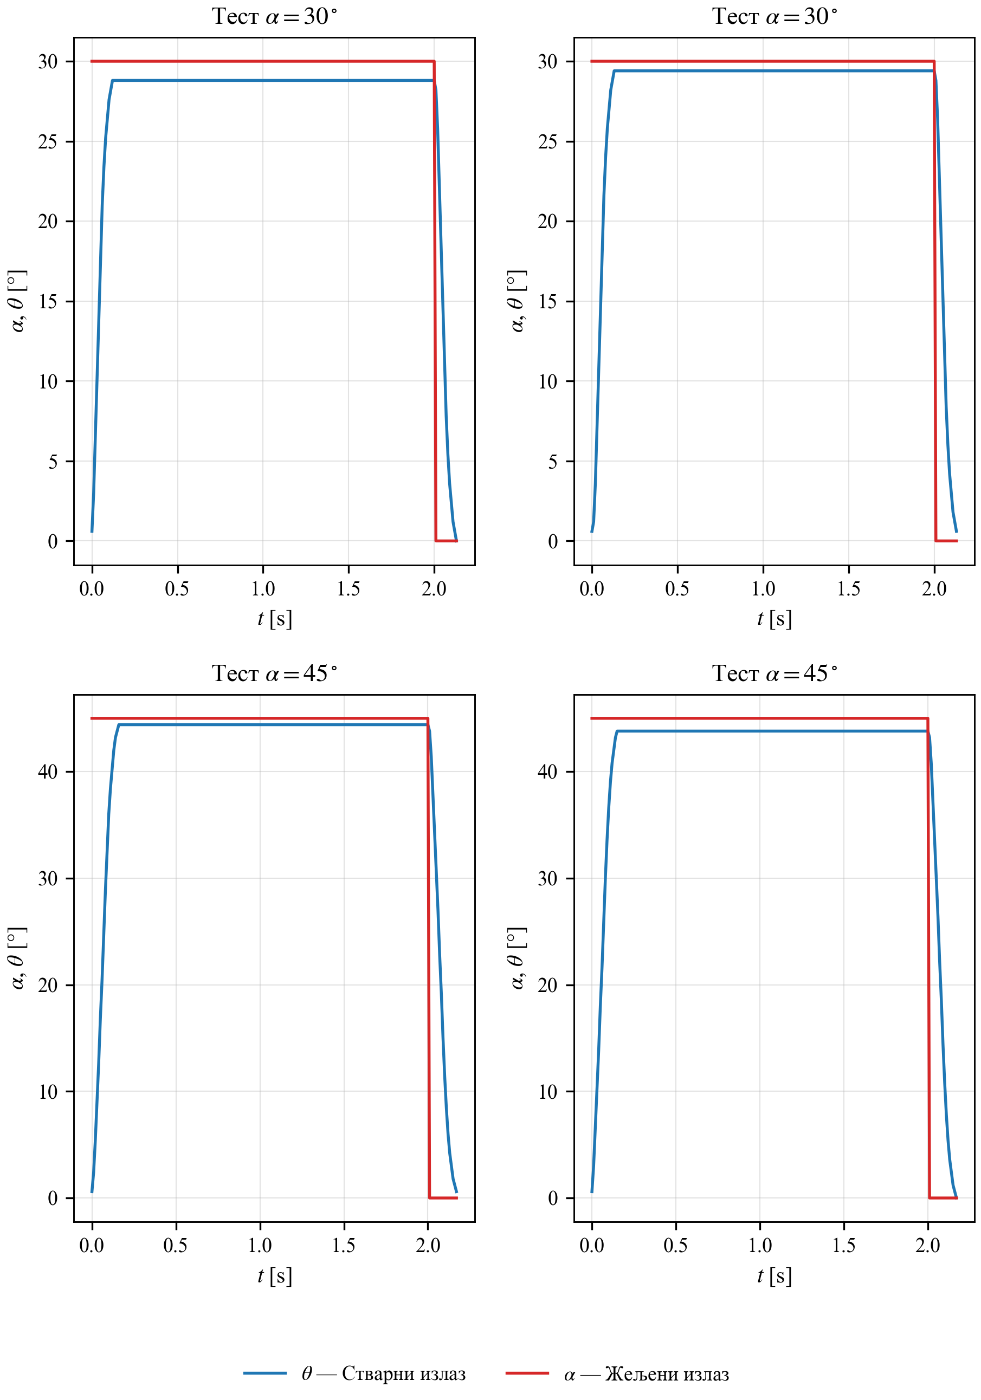
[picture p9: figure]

Слика 3.12г – Графички приказ података прикупљених експериментом 1

Слика 3.13a – Графички приказ података прикупљених експериментом 2

Слика 3.13б – Графички приказ података прикупљених експериментом 2

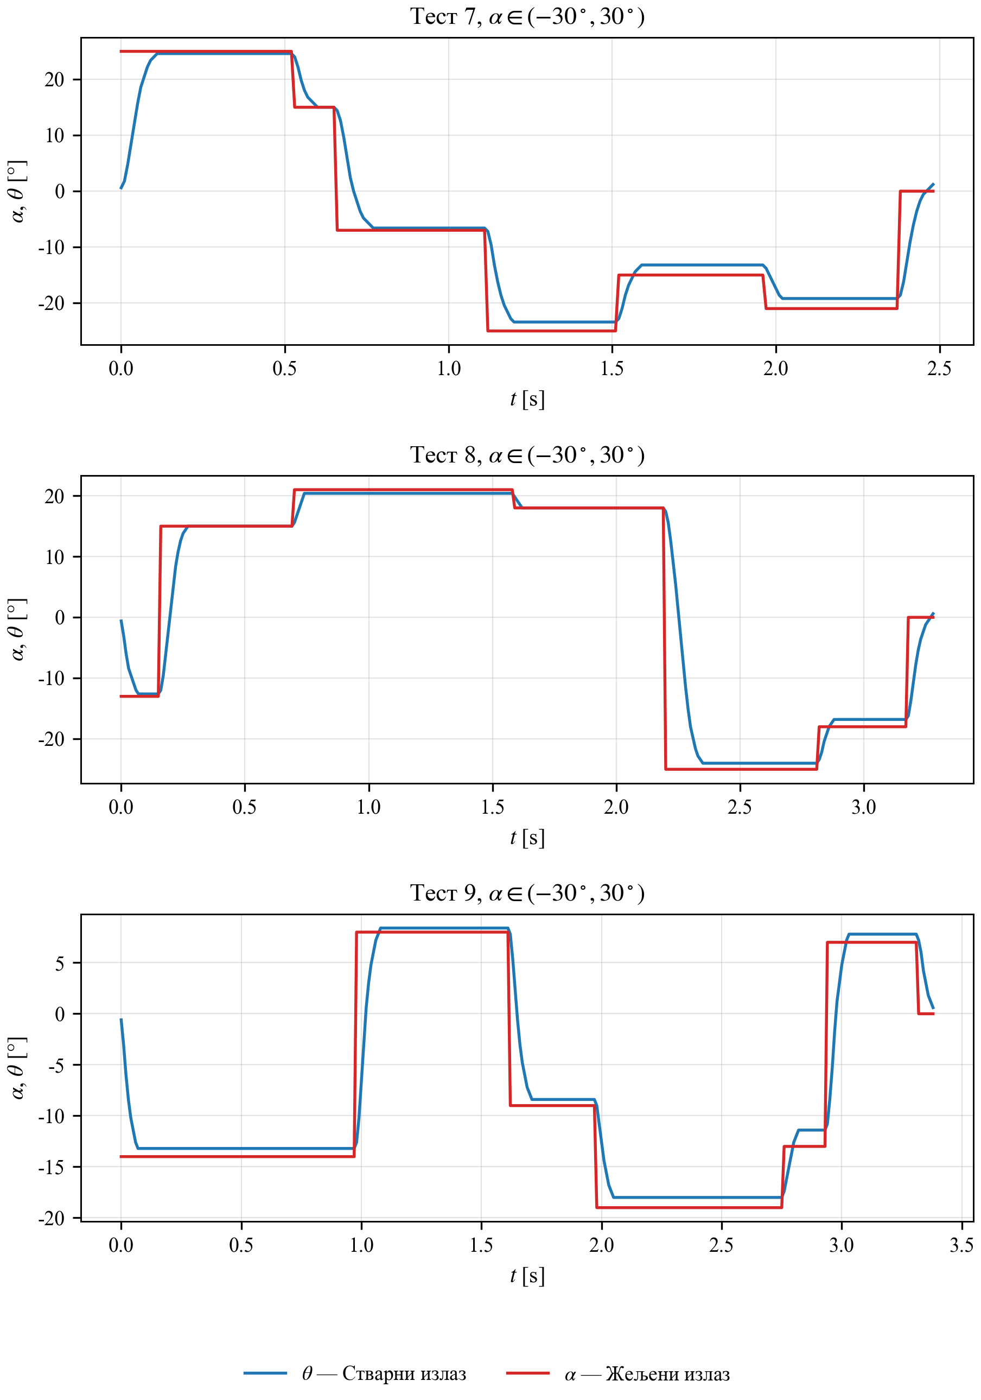
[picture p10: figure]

Слика 3.13в – Графички приказ података прикупљених експериментом 2

Слика 3.13г – Графички приказ података прикупљених експериментом 2

Слика 3.13д – Графички приказ података прикупљених експериментом 2

Слика 3.13ђ – Графички приказ података прикупљених експериментом 2

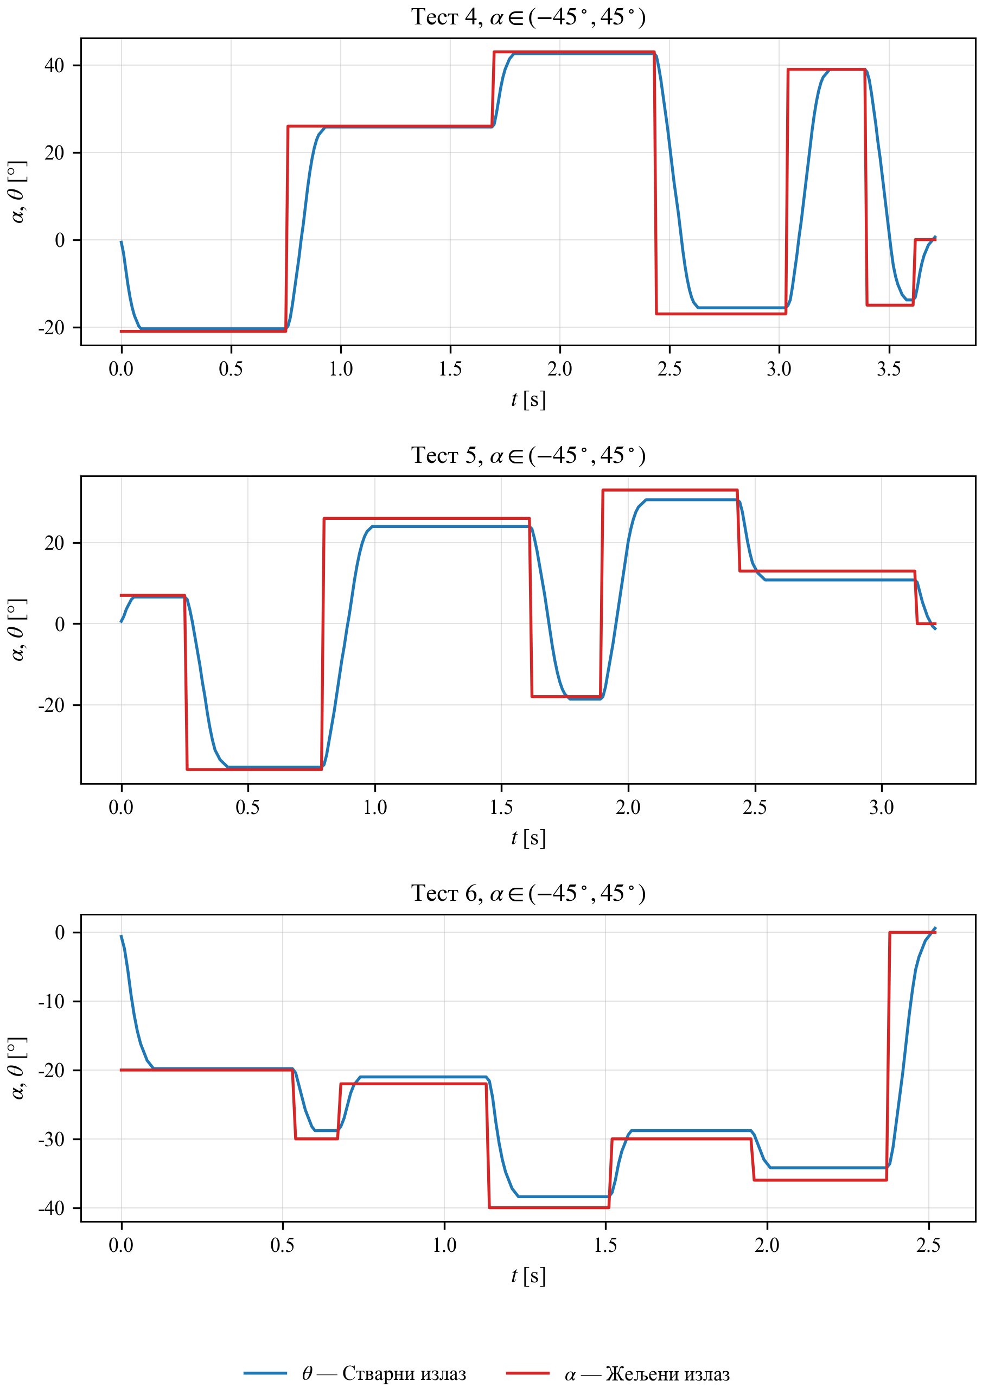
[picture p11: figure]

Слика 3.13е – Графички приказ података прикупљених експериментом 2

Слика 3.13ж – Графички приказ података прикупљених експериментом 2

Слика 3.13з – Графички приказ података прикупљених експериментом 2

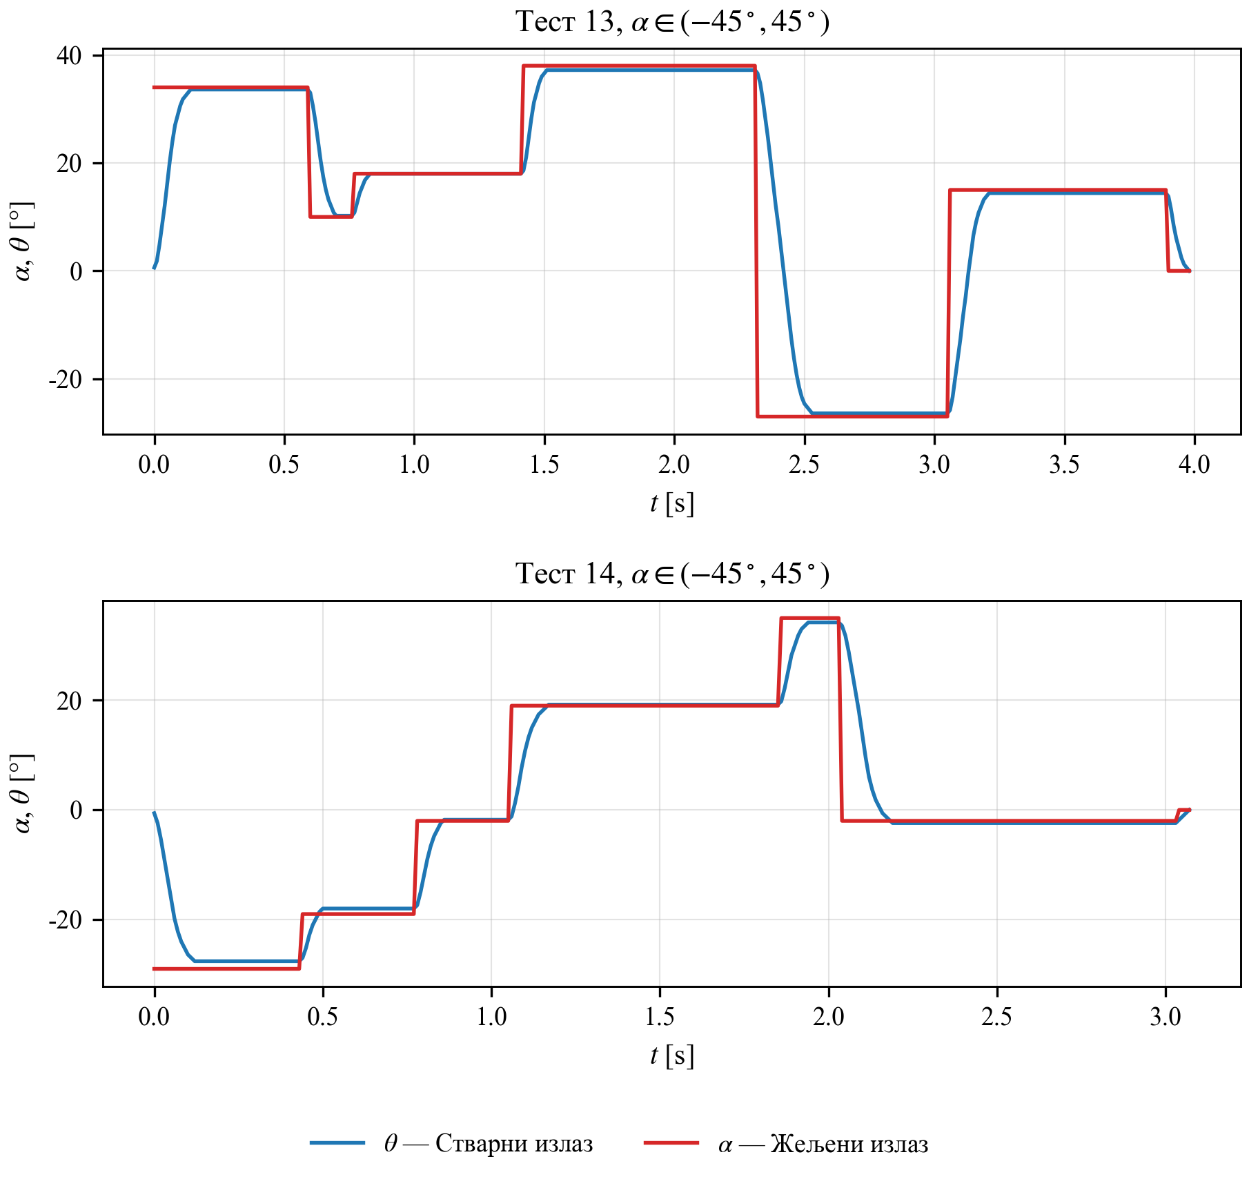
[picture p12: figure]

Слика 3.13и – Графички приказ података прикупљених експериментом 2

### 3.2.2. Идентификација система методом сиве кутије

Серво мотор једносмерне струје се састоји од мотора једносмерне струје, који је директно спрегнут са редуктором, позиција излазног вратила се очитава помоћу потенциометра и сам серво мотор поседује свој контролер са управљачким алгоритмом.

На основу претходно реченог може се закључити да је систем затворен и да се до структуре модела можемо доћи налажењем општег математичког модела затвореног система електро мотора једносмерне струје са редуктором.

#### 3.2.2.1. Општи математички модел електро мотора једносмерне струје са редуктором

Шема електро мотора једносмерне струје са редуктором је приказана на слици 3.18, где су:

- Vm – напон,
- Im – струја,
- Rm – отпорност мотора,
- Lm – индуктивност мотора,
- km – константа електромоторне силе мотора,
- eb – повратни напон електромотора,
- ωm – угаона брзина вратила мотора једносмерне струје,
- ωl – угаона брзина излазног вратила мотора са редуктором,
- τl – обртни момент излазног вратила мотора са редуктором,
- Jx – момент инерције компоненте x, где је x = m, l,
- Bx – вискозно трење, где је x = m, l и
- Nx – број зубаца на зупчанику х, где је x = 1, 2, 3, 4.

Слика 3.14 – Шема спреге електро мотора једносмерне струје са редуктором

Моделовање електричног дела система

Кренувши од другог Кирховог закона који гласи “Сума свих напона у контури је једнака нули”, долази се до следеће једначине:

V_m (t)- R_m I_m - L_m (dI_m (t))/(dt)-k_m ω_m (t)= 0. (3.2.1)

Узевши у обзир да је индуктивност мотора много мања од отпорности мотора, претходна једначина може се записати у следећем облику:

V_m (t)- R_m I_m - L_m (dI_m (t))/(dt)-k_m ω_m (t)= 0, (3.2.2)

односно:

I_m (t)= (V_m (t)-k_m ω_m (t)). (3.2.3)

Моделовање механичког дела система

Кренувши од другог Њутновог закона који за ротационо кретање гласи “Угаоно убрзање које при кретању добије једно тело сразмерно је интензитету обртног момента који делује на њега, а обрнуто сразмерно моменту инерције тела”

J α= τ, (3.2.4)

може се доћи до следећих једначина:

J_l (dω_l (t))/(dt) + B_l ω_l (t)= τ_l (t), (3.2.5)

J_m (dω_m (t))/(dt) +B_m ω_m (t)+τ_(ml) (t)= τ_m (t), (3.2.6)

где је (3.2.4) једначина за обртни момент излазног вратила система, а (3.2.5) једначина обртног момента на излазном вратилу електро мотора. Једначина обртног момента излазног вратила система може се записати и у следећем облику:

τ_l (t)= η_g K_g τ_(ml) (t), (3.2.7)

где су:

K_(gi) = (N_2)/(N_1); K_(ge) = (N_4)/(N_3); K_g =K_(ge) K_(gi) . (3.2.8)

За потребе даљег решавања једначина (3.2.6) је усвојена у следећем облику:

τ_(ml) (t)=(τ_l (t))/(η_g K_g). (3.2.9)

Зависност промене угла излазног вратила мотора у односу на промену угла излазног вратила система мотора са редуктором може се представити следећом једначином:

θ_m (t)= K_g θ_l (t), (3.2.10)

одакле следи да зависност њихових угаоних брзина може бити исказана следећом једначином:

ω_m (t)= K_g ω_l (t) . (3.2.11)

односно на основу претходних релација може се доћи до следећег израза:

J_m K_g (dω_l (t))/(dt) +B_m K_g ω_l (t)+(J_l (dω_l (t))/(dt) + B_l ω_l (t))/(η_g K_g)=τ_m (t), (3.2.12)

и ако се уведу смене:

J_(eq) = η_g K_g ^2 J_m +J_l и (3.2.13)

B_(eq) =η_g K_g ^2 B_m +B_l , (3.2.14)

доћи ће се до следеће једначине:

J_(eq) (dω_l (t))/(dt) + B_(eq) ω_l (t)= η_g K_g τ_m (t). (3.2.15)

Комбиновање електричног и механичког система

Комбиновањем претходна два система доћи ће се до општег математичког модела електро мотора једносмерне струје са редуктором.

Обртни момент мотора може се представити и следећом једначином:

τ_m (t)= η_m k_t I_m (t), (3.2.16)

која се на основу једначине (3.2.2) може развити у облик:

τ_m (t)= (η_m k_t (V_m (t) - k_m ω_m (t)))/(R_m) (3.2.17)

односно, на основу (3.2.10):

τ_m (t)= (η_m k_t (V_m (t) - k_m K_g ω_l (t)))/(R_m). (3.2.18)

Убацивањем једначине (3.2.14) у претходну добија се:

J_(eq) (dω_l (t))/(dt) + B_(eq) ω_l (t) =(η_g K_g η_m k_t (V_m (t) - k_m K_g ω_l (t)))/(R_m). (3.2.19)

Док сређивањем једначине (3.2.18) се добија:

J_(eq) d/(dt)ω_l (t) + ( (k_m K_g^2 k_t η_g η_m)/(R_m)+B_(eq) )ω_l (t)= (η_g K_g η_m k_t)/(R_m) V_m (t) (3.2.20)

односно:

J_(eq) d/(dt)ω_l (t)+B_(eq,v) ω_l (t)= A_m V_m (t) , (3.2.21)

где је:

B_(eq,v) =(k_m K_g^2 k_t η_g η_m)/(R_m)+B_(eq) и (3.2.22)

A_m = (η_g K_g η_m k_t)/(R_m). (3.2.23)

Једначина (3.2.20) представља математички модел електро мотора једносмерне струје са редуктором и применом леве Лапласове трансформације може се свести на следећи облик:

J_(eq) ω_l (s)+B_(eq,v) ω_l (s)= A_m V_m (s), (3.2.24)

односно:

(ω(s))/(V_(m(s)))=(A_m)/(J_(eq) s +B_(eq,v)) , (3.2.25)

Узевши у обзир да се у свим експериментима управљало позицијом серво мотора, претходна једначина је интеграљена, чиме је добијена преносна функција промене угла излазног вратила мотора једносмерне струје са редуктором у зависности од напона:

W(s)= (θ_l (s))/(V_m (s))=(A_m)/(s(J_(eq) s + B_(eq,v) )) = (b_0)/(s + a_0) 1/s (3.2.26)

#### 3.2.2.2. Одређивање математичког модела

Познато је да је серво мотор, сам по себи, један затворен систем. На улаз серво мотора је потребно довести одговарајући напон и он би на основу тог напона ротира излазно вратило за одређени угао. Узимајући у обзир да је за експерименте коришћена библиотека која омогућава да се за жељену вредност излаза зада жељена позиција излазног вратила серво мотора за преносну функцију је усвојен количник стварне и жељене позиције излазног вратила серво мотора:

W(s)= (θ_l (s))/(Х_(iz) (s)). (3.2.27)

Структура и принцип рада комерцијалног серво мотора једносмерне струје детаљно су приказани у истраживачком раду Yoonky Hawng, Yuki Minami и Makato Ishikawа, под насловом Виртуални сензор обртног момента за јефтине серво моторе једносмерне струје засноване на идентификацији динамичког система са параметријским ограничењем (енг. Virtual Torque Sensor for Low-Cost RC Servo Motors Based on Dynamic System Identification Utilizing Parametric Constraints).

Алгоритам рада серво мотора и сликовита шема приказани су на слици 3.19, док је блок дијаграм серво мотора једносмерне струје приказан на слици 3.20.

Слика 3.15 – Алгоритам рада серво мотора једносмерне струје и сликовита шема

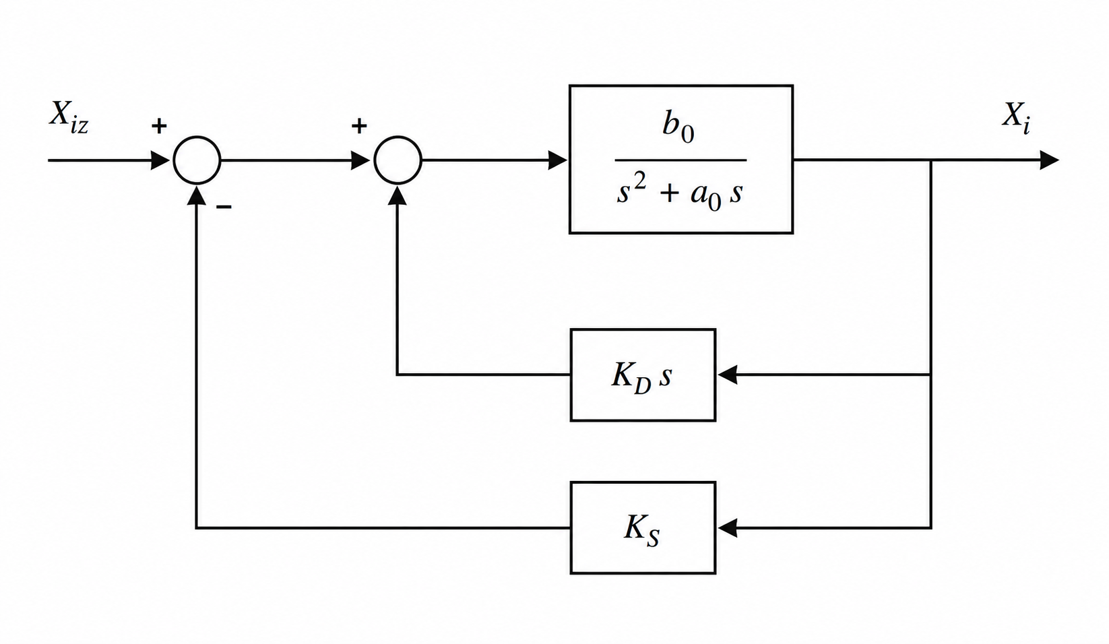
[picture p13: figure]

Слика 3.16 – Блок дијаграм серво мотора једносмерне струје

Сређивањем блок дијаграма са слике 3.20 долазимо до следеће преносне функције:

W(s)= (θ_l (s))/(Х_(иж) (s))= (b_0)/(s^2 + s (a_0 - K_D b_0 ) + K_s b_0) . (3.2.28)

Естимација параметара и први део валидације је одређен помоћу Matlab скрипт tfEstimation.m.

Скрипта — tfEstimation.m

close all

clear all

clc

sysData = struct();

dir_path = "..\Ball_And_Beam\System_Identification\Data\Encoder_data\Test_";

data_path = "\Processed\Test_";

% Polovi i nule

np = 2; % broj polova

nz = 0; % broj nula

file_path = "..\Ball_And_Beam\System_Identification\Data\Estimation_data\GreyBox\Model_1.json";

% Estimacija prenosne funkcije

for idx = 1:2

for jdx = 0:29

try

final_path = dir_path + int2str(idx) + data_path + int2str(jdx) + ".csv";

T = readtable(final_path, 'ReadVariableNames', true);

% Remove everything after t>= 2s and NaN values

toDelete = T.Time_s >= 2.0;

T(toDelete, :) = [];

T = rmmissing(T);

% Estimate tf and save num and den of sys

data = iddata(T.Angles, T.PWM, 0.01);

sys = tfest(data, np, nz);

test_no = sprintf('test_%d_%d', idx, jdx);

sysData.(test_no).num = sys.Numerator;

sysData.(test_no).den = sys.Denominator;

% Simulate and show on plot for quick validation

simTime = 0:0.01:length(T.PWM)/100-0.01;

[y, tout] = lsim(sys, T.PWM, simTime);

figure(idx*100+jdx);

plot(tout, y, T.Time_s, T.Angles);

grid on;

catch ME

if (strcmp(ME.identifier, 'MATLAB:readtable:OpenFailed'))

;

else

disp(ME)

end

end

end

end

% Validate data

keys = fieldnames(sysData);

for idx = 1:length(keys)

curent_key = string(keys(idx));

MSE_data = Validate(sysData.(curent_key).num, sysData.(curent_key).den);

sysData.(curent_key).MSE = MSE_data;

end

jsonData = jsonencode(sysData);

fileID = fopen(file_path, 'w');

if fileID == -1

error('Cannot open file for writing: %s', file_path);

end

fprintf(fileID, '%s', jsonData);

fclose(fileID);

Функција — Validation.m

function [MSE] = Validate(num,den)

%VALIDATE Summary of this function goes here

% Detailed explanation goes here

dir_path = "..\Ball_And_Beam\System_Identification\Data\Encoder_data\Validation_data\Dir_";

errorData= struct();

sys = tf(num, den);

for i = 1:2

for j = 0:8

try

final_path = dir_path + int2str(i) + '\Val_Data_' + int2str(j) + '.csv';

T = readtable(final_path, 'ReadVariableNames', true);

[y, ] = lsim(sys, T.PWM, T.Time_s);

test_no = sprintf('mse_%d_%d', i, j);

errorData.(test_no) = immse(T.Angles, y);

catch ME

if (strcmp(ME.identifier, 'MATLAB:readtable:OpenFailed'))

;

else

disp(ME)

end

end

end

end

MSE = errorData;

end

Скрипт може да се подели у неколико делова:

- иницијализација – део на почетку скрипта где се дефинишу бројеви полова и нула преносне функције (np и nz),
- естимација параметара преносне функције – део где се на основу података сваког случаја прве групе експеримента естимирају параметри преносне функције,
- валидација модела – циљ овог дела јесте поређење излаза модела са излазима сваког случаја једног дела друге групе експеримента (-30, 30). Излаз ове функције је низ средњих квадратних грешака.
- чување података – овај део скрипта је задужен за креирање датотеке json формата и чување естимираних вредности модела и низова средњих квадратних грешака у истој датотеци.

За даљу анализу претходно сачуване датотеке искоришћена је скрипта Data_visualization.py (код овог скрипта се може наћи у додатку Б). Скрипт за сваки модел рачуна просечну, медијану и најгору средњу квадратну грешку и рангира преносне функције. Такође, даје и графички приказ расподела средњих квадратних грешака (слика 3.21), са којег можемо закључити да су експериментални подаци задовољавајућег квалитета за идентификацију мотора и омогућава предселекцију кандидата за даљи рад. Као финални излаз ова скрипт даје и коефицијенте пет најбољих преносних функција (табела 3.1).

Преносна функција | Коефицијенти бројиоца | Коефицијенти имениоца
1 | 569.62 | 1, 38.54, 593.73
2 | 569.32 | 1, 38.51, 593.46
3 | 566.56 | 1, 38.71, 590.51
4 | 620.45 | 1, 39.94, 637.82
5 | 534.42 | 1, 37.08, 549.42

Табела пет најбољих преносних функција – Табела 3.1

Слика 3.17 – График расподеле средњих квадратних грешака по моделу

Три изабране преносне функције даље су анализиране скриптом tfValidation.m на скуповима података скупљених другом групом експеримента. За сваки случај симулиран је одзив модела и упоређен се мереним, стварним, одзивом. Резултати су приказани графицима упоређених одзива (сликe 3.18а, 3.18б, 3.18в) и дијаграмима резидуала (слике 3.19а, 3.19б, 3.19в). На сликама одзива:

- ti је одзив стварног система
- αtf1 је одзив преносне функције 1 из табеле 3.1,
- αtf4 је одзив преносне функције 4 из табеле 3.1 и
- αtf5 је одзив преносне функције 5 из табеле 3.1.

Слика 3.18а – Графички приказ стварног одзива и одзива модела

Слика 3.18б – Графички приказ стварног одзива и одзива модела

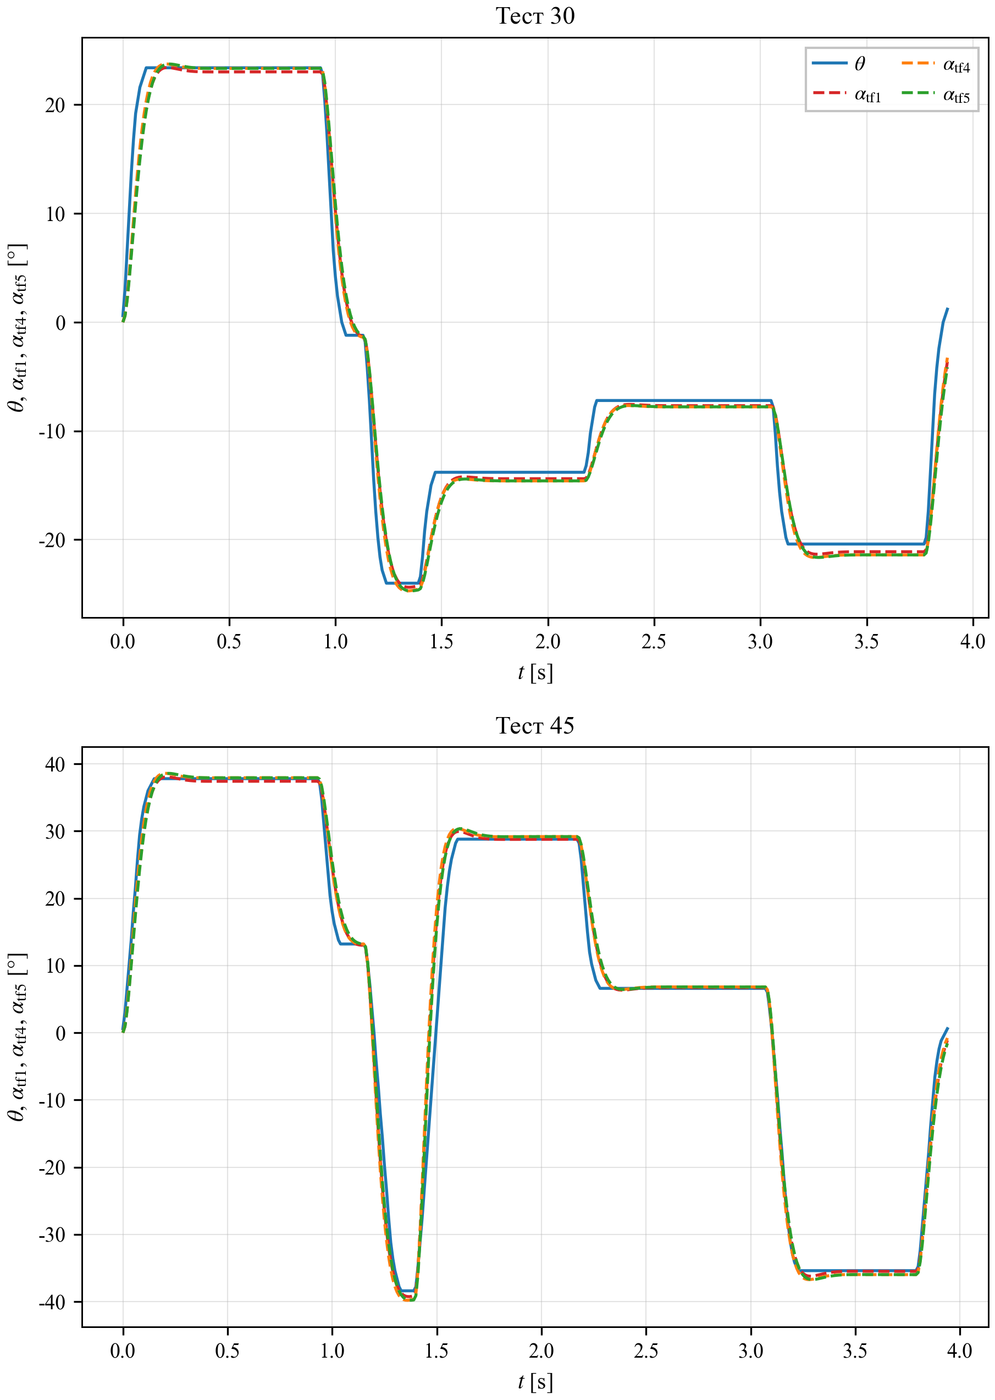
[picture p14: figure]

Слика 3.18в – Графички приказ стварног одзива и одзива модела

Слика 3.19а – Дијаграм резидуала

Слика 3.19б – Дијаграм резидуала

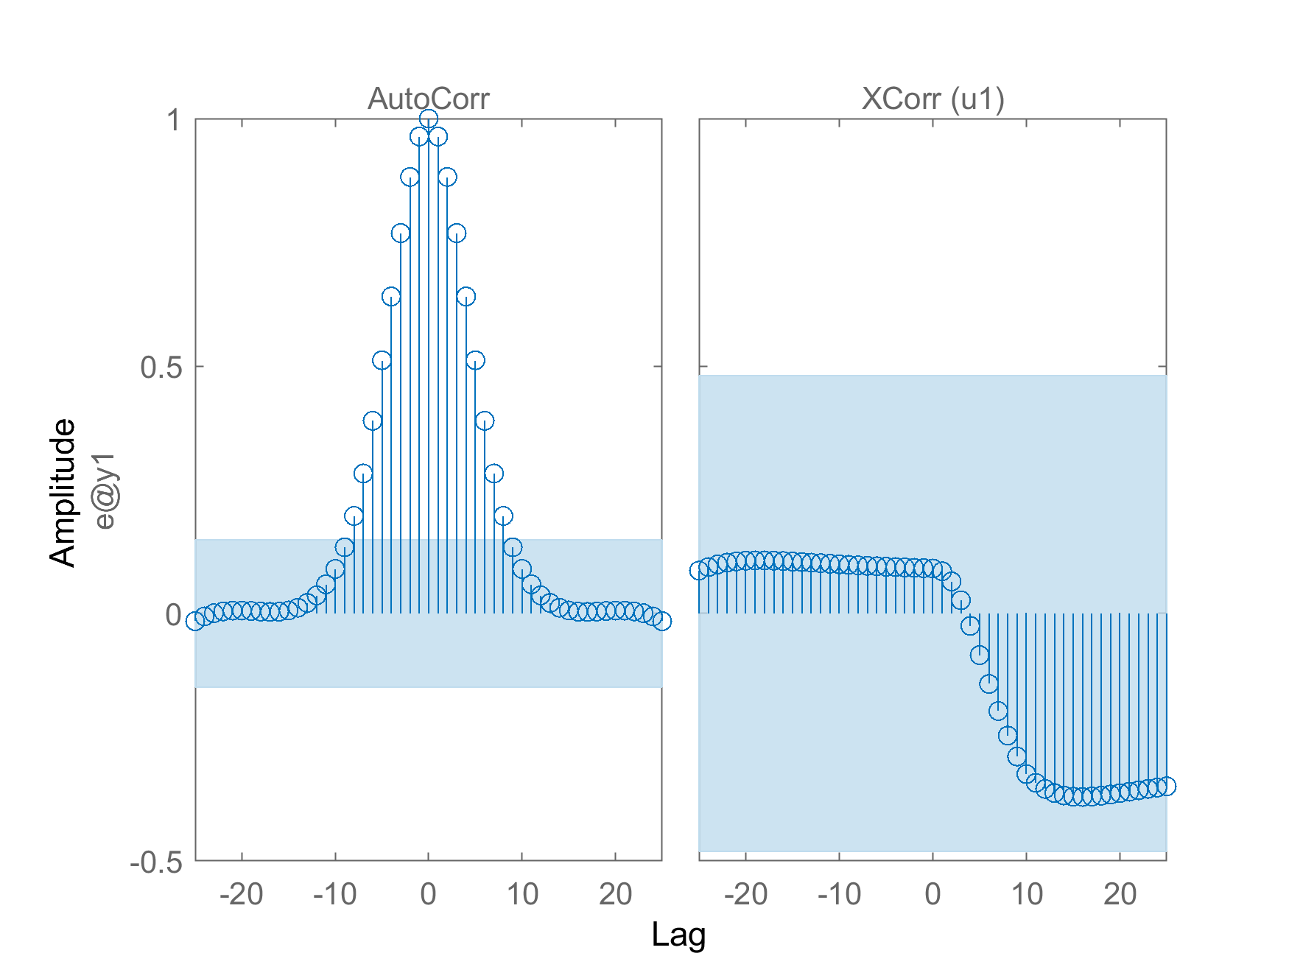
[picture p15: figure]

Слика 3.19в – Дијаграм резидуала

Са графика и дијаграма може се закључити да сва три модела су показала готово идентично праћење у временском домену и резидуалну статистику, што указује да је идентификована динамика робусна, а неосетљива на специфични скуп параметара.

За даљи рад изабрана је преносна функција 1 (3.2.29). Анализа резидуала овог модела показује да унакрсна корелација између резидуала и улазног сигнала референце остаје унутар интервала поверења на свим валидационим скуповима, чиме се потврђује да је улазно-излазна веза адекватно описана. Аутокорелација резидуала, међутим, систематски прелази границе интервала поверења, посебно током прелазног процеса, што указује да модел другог реда не обухвата целокупну динамику излаза и да преостала грешка није потпуно случајна. Иако анализа резидуала указује на присуство динамике вишег реда или нелинеарних ефеката у систему серво мотора, прихватљиво је усвојити ову преносну функцију као математички модел и користити је у даљем раду.

W(s)= 569.62/(s^2 + 38.54 s + 593.73) . (3.2.29)

### 3.2.3. Идентификација система методом црне кутије

У овом делу покушаћемо да одредимо математички модел серво мотора користећи метод црне кутије. Водећи се научним радовима:

- Deep Learning and System Identification, чији су аутори Lennart Ljung, Carl Andersson, Koen Tiels и Thomas B. Schon и
- Cascade Forward Neural Network for Time Series Prediction, чији су аутори Budi Warsito, Rukun Santoso, Suparti, Hasbi Yasin.

одлучено је да се за идентификацију система користи вишеслојна каскадна неуронска мрежа у комбинацији са нелинеарним ауторегресивним моделом са егзогеним улазима (NARX).

#### 3.2.3.1. Вишеслојна каскадна неуронска мрежа без повратне спреге

Како би лакше објаснили вишеслојну каскадну неуронску мрежу без повратне спреге кренимо од “обичне” вишеслојне неуронске мреже без повратне спреге.

Због једноставности објашњења претпоставимо да имамо два улаза, један излаз и два скривена слоја како на слици 3.24, такође претпоставимо да сви неурони имају исту активациону функцију f и усвојимо следећу нотацију:

- xp — p-ти улаз неуронске мреже,
- zij — излаз неурона у скривеном слоју i,
- w^ijk — тежинa j-тог неурона у i-том скривеном слоју и
- y — излаз неуронске мреже,

где су i, j, k, p = 1, 2, 3, 4, ..., n.

Слика 3.20 – Вишеслојна неуронска мрежа без повратне спреге

Излаз једног неурона првог слоја је дат следећом једначином:

z_(1j) = f(w_(j1)^1 x_1 +w_(j2)^1 x_2 )= f([w_(j1)^1 w_(j2)^1 ][, x_1 , x_2 ]) . (3.2.30)

Узимајући у обзир да први слој садржи три неурона можемо представити излаз целог слоја у следећем облику:

z_1 =[, z_11 , , z_12 , z_13 ]=f(w^1 x). (3.2.31)

Други и излазни слој прате исти тренд и могу се представити следећим једначинама:

z_2 =[, z_21 , z_22 ] = f(w^2 z_1 ) и (3.2.32)

y=f(w^3 z_2 ). (3.2.33)

Вишеслојна каскадна неуронска мрежа без повратне спреге се разликује од претходно објашњене мреже у начину на који су слојеви повезани. Код каскадне мреже слој n+2 (n = 0, 1, 2, 3, ...) није повезан само са претходним слојем, већ са свим претходним слојевима.

Претпоставимо поново да наша мрежа има два улаза, један излаз и два скривена слоја као на слици 3.24, али усвојимо топологију каскадне неуронске мреже, слика 3.25. Такође, претпоставимо да сви неурони имају исту активациону функцију f и задржимо исту нотацију.

Слика 3.21 – Вишеслојна каскадна неуронска мрежа без повратне спреге

Јасно је да је и у овом случају излаз једног неурона у првом слоју дат једначином (3.2.32), односно излаз целог слоја је дат изразом (3.2.33). Разлика од претходне мреже се може уочити у другом слоју, где је излаз једног неурона у овом слоју дат једначином:

z_(2ј) = f(w_(ј1)^2 x_1 +w_(ј2)^2 x_2 +w_(ј3)^2 z_11 +w_(ј4)^2 z_12 +w_(ј5)^2 z_13 ) , (3.2.34)

односно:

z_(2ј) = f([w_(ј1)^2 w_(ј2)^2 w_(ј3)^2 w_(ј4)^2 w_(ј5)^2 ][, x_1 , , x_2 , , z_11 , , z_12 , z_13 ]) . (3.2.35)

Узимајући у обзир да други слој садржи два неурона, излаз целог слоја можемо представити у следећем облику:

z_2 =[, z_21 , z_22 ]=f(w^2 [, x, z_1 ]). (3.2.36)

Пратећи исти тренд јасно је да поред излаза другог слоја z2, утицај на излаз ове мреже имати ће и улаз x и излаз првог слоја z1 и да једначина излаза бити:

y=f(w^3 [, x, , z_1 , z_2 ]). (3.2.37)

#### 3.2.3.2. Дефиниције ауторегресивних модела

Ауторегресивни модели су основни алати за моделирање и анализу динамичких система, описујући како тренутни излаз система зависи од његових претходних излаза. Они играју кључну улогу у хватању унутрашње динамике система и често се проширују укључивањем спољних улаза, што доводи до свеобухватнијих модела. У области идентификације система, ауторегресивни модели се користе за креирање математичких представљања система заснованих на посматраним подацима. Ови модели су посебно ефикасни за системе где се понашање може предвидети на основу претходних стања, са фокусом на разумевање унутрашње динамике. Када су присутни спољни фактори, ауторегресивне компоненте се могу комбиновати са егзогеним улазима, формирајући напредније моделе као што су ARX или ARMAX, који укључују и унутрашњу динамику и спољне утицаје.

Дефиниција 9 Ауторегресивни (AR) модел је динамички модел који описује тренутну вредност излазне променљиве као линеарну комбинацију њених претходних вредности. У идентификацији система аутоматског управљања користи се за описивање динамике система на основу претходних вредности излаза, без непосредног укључивања улазног сигнала. Општи облик ауторегресивног модела p -тог реда дат је једначином:

y(t)= c + ∑_(i=1)^p φ_i y(t-i)+ε(t) . (3.2.38)

Где је:

- y(t) — излаз,
- c — константа,
- φi — i-ти коефицијент модела,
- ε(t) — грешка,
- p — ред модела, који показује број коришћених претходних вредности.

Дефиниција 10 Спољашња улазна величина представља све познате улазне величине система, односно објекта, које битно утичу на рад самог система.

Да сумирамо, спољашња улазна величина се односи и на све жељене вредности излазне величине и све мерене/познате величине поремећаја.

Дефиниција 11 Ауторегресивни модел са спољашњим улазом (ARX модел) је тип линеарног динамичког модела који се користи у идентификацији система и комбинује ауторегресивни део (AR) са спољашњим улазом (X). Општи облик ARX модела је:

y(t)=∑_(i=1)^(n_a) a_i y(t-i) +∑_(j=1)^(n_b) b_i u(t-j)+ε(t). (3.3.39)

Где је:

- y(t) — излаз,
- u(t−j) — спољашњи улаз,
- ai — коефицијент за ауторегресивне чланове, где је i = 1, 2, ..., na,
- bj — коефицијент за егзогене улазе, где је j = 1, 2, ..., nb,
- na — број претходних вредности излаза (ред ауторегресије),
- nb — број претходних вредности улаза које се узимају у обзир,
- ε(t) — грешка која са собом носи информације о свим не мереним улазима (углавном поремећајима).

Дефиниција 12 Нелинеарни ауторегресивни модел са спољашњим улазима (NARX) је врста динамичког нелинеарног модела који се обично користи за моделирање система са информацијама о прошлим улазима и прошлим излазима који утичу на будуће излазе. Овај модел је описан следећом једначином:

y(t)= f(y(t-1), y (t-2), ..., y(t-n_y ), u(t-1), u(t-2), ..., u)(t-n_u )+ ε(t), (3.2.40)

где су:

- y(t) — излаз,
- u(t) — улаз,
- f(•) — функција нелинеарности и
- ε(t) — грешка која са собом носи информације о свим не мереним улазима (углавном поремећајима).

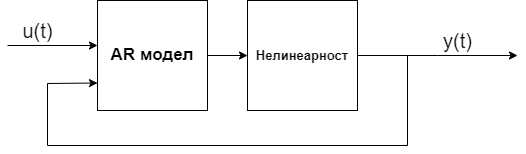
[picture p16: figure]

Слика 3.22 – Графички приказ нелинеарног ауторегресивног модела са спољшњим улазима

#### 3.2.3.3. Идентификација система

За потребе овог задатка искористили смо податке из другог експеримента, где смо насумично одабрали двадесет два случаја и искористили за обучавање мреже и естимацију модела, а осталих седам смо искористили за валидацију.

За идентификацију и валидацију модела искористили смо Matlab скрипт bbModelEstimation.m где смо за модела изабрали нелинеарни ауторегресивни модел са спољашњим улазом, а за излазну функцију, односно нелинеарност, изабрали вишеслојну каскадну неуронску мрежу без повратне спреге. Кроз пар итерација дошли смо до конфигурације каскадне мреже која има пет скривених слојева са следећим бројем неурона [2, 3, 4, 3, 2] и ауторегресивног модела са спољашњим улазом који се може описати следећом једначином:

y(t)=∑_(i=1)^4 a_i y(t-i) +∑_(j=1)^4 b_i u(t-j). (3.2.41)

Скрипта — bbModelEstimation.m

close all

clear all

clc

training_data_path = "..\Ball_And_Beam\System_Identification\Matlab_Scripts\Black_Box\TestData.csv";

validatio_data_path = "..\Ball_And_Beam\System_Identification\Matlab_Scripts\Black_Box\ValidationData.csv";

T = readtable(training_data_path, 'ReadVariableNames', true);

training_data = iddata(T.Angles, T.PWM, 0.01);

net = cascadeforwardnet([2,3,4,3,2]);

N2 = neuralnet(net);

sys = nlarx(training_data, [4 4 0], N2);

% Validate against training data

figure(1);

compare(training_data, sys);

figure(2);

resid(training_data, sys);

% Validate against validation data

T = readtable(validatio_data_path, 'ReadVariableNames', true);

validatio_data = iddata(T.Angles, T.PWM, 0.01);

figure(3);

compare(validatio_data, sys);

figure(4);

resid(validatio_data, sys);

Након естимације, модел је проверен на независном скупу од седам валидационих експеримената.

Слика 3.23а – Поређење стварног одзива и одзива модел одређеним методом црне кутије

Слика 3.23б – Поређење стварног одзива и одзива модел одређеним методом црне кутије

Слика 3.23в – Поређење стварног одзива и одзива модел одређеним методом црне кутије

Слика 3.23г – Поређење стварног одзива и одзива модел одређеним методом црне кутије

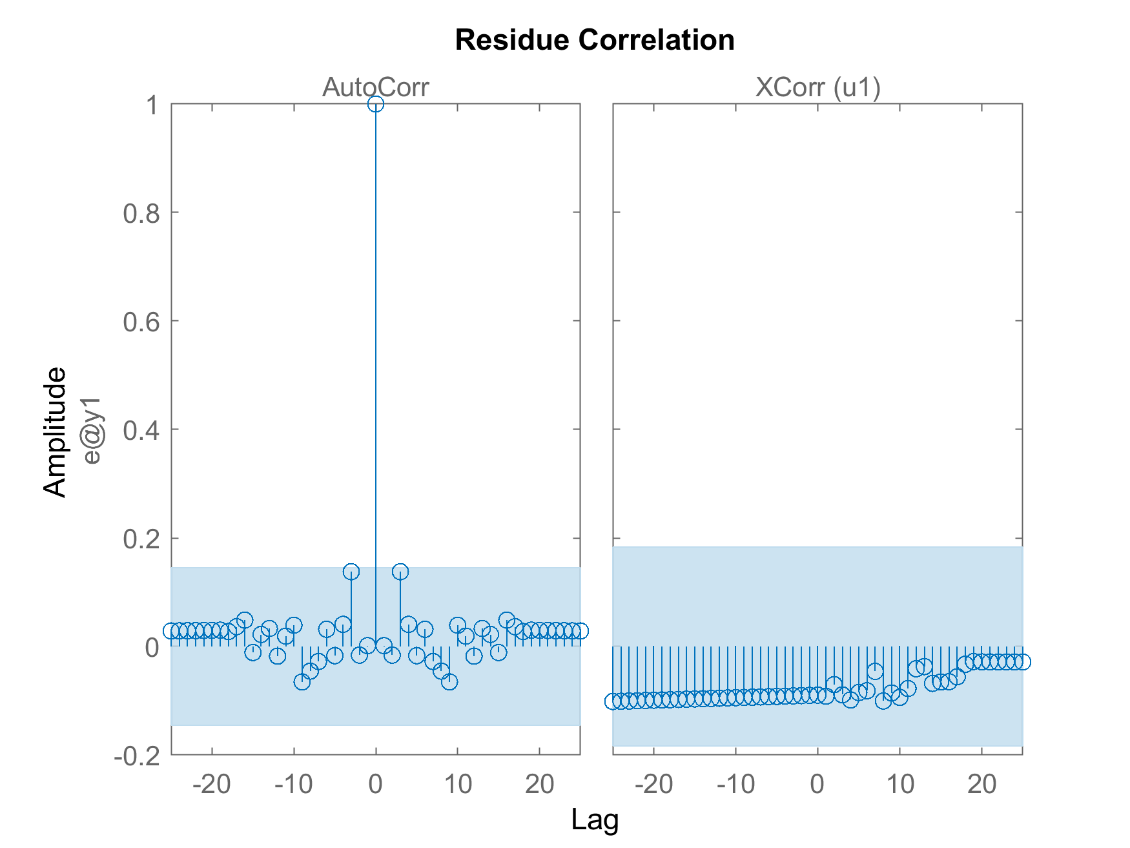
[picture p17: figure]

Слика 3.24 – Дијаграм резидуала

На свим случајевима модел прати облик одзива, а степен преклапања је нешто већи од 93% и на скупу за обучавање и на валидационом скупу. У односу на модел сиве кутије, овде је преклапање веће (преко 93% насупrot oko 87%), а преостала грешка модела нема значајне корелације ни са собом ни са улазним сигналом. NARX модел не захтева унапред задату структуру мотора, већ директно учи улазно-излазну везу из података, па имплицитно обухвата нелинеарности и ефекте унутрашњег серво регулатора које линеарни модел не обухвата.

# 4. Пројектовање и имплементација регулатора

## 4.1. Анализа и испитивање система

Пре пројектовања и имплементације регулатора потребно је испитати и анализирати цео систем. У нашем случају систем се састоји из два дела, лопте на шини и серво мотора. Чије смо математичке моделе одредили и анализирали у претходном делу.

У овом делу упоредићемо линеаризовани и нелинеарни модел лопте на шини са стварним системом. И на основу тог поређења одабрати модел који ћемо касније искористи за пројектовање регулатора.

###### Нелинеарни, линеаризовани и стварни систем лопте на шини

Као што је напоменуто у уводу, математички модел лопте на шини је одређен у претходном поглављу, прецизније у поглављу 3.1 Једначина кретање лопте на шини. У овом поглављу једначина је упрошћена и дата у облику преносне функције, изразом 3.1.19. Међутим, кретње лопте на шини може се представити и једначинама 3.1.6 и 3.1.12.

Користећи софтверски алат Simulink за даље потребе мастер рада, анализирали смо:

- нелинеарни систем лопте на шини без серво мотора,
- линеаризовани систем лопте на шини без серво мотора,
- нелинеарни систем лопте на шини са преносном функцијом серво мотора,
- линеаризовани систем лопте на шини са преносном функцијом серво мотора,
- нелинеаризовани систем лопте на шини са нелинеарни моделом серво мотора и
- линеаризовани систем лопте на шини са нелинеарним моделом серво мотора.

У обзир су узети и отворени и затворени систем. При анализи отвореног система посматран је само одзив система у временском домену, док су при анализи затвореног система разматрани и одзив система у временском домену и промена угла серво мотора.

Приликом креирања блок дијаграма у програмском пакету Simulink усвојено су следеће вредности параметара:

- опсег угла серво мотора: од -45° до 45°,
- опсег умерене позиције лопте: од 0mm до 400mm,
- почетна позиција лопте: 100mm и
- референта (жељена) позиција лопте: 250mm.

Блок дијаграми затворених система су приказани на наредним сликама и то редом:

- Нелинеарни и линеаризовани модели лопте на шини – слика 4.1,
- Нелинеарни и линеаризовани модели лопте на шини у спрези са математичким моделом серво мотора одређеним методом сиве кутије – слика 4.2 и
- Нелинеарни и линеаризовани модели лопте на шини у спрези са математичким моделом серво мотора одређеним методом црне кутије – слика 4.3.

Слика 4.1 – Нелинеарни и линеаризовани модели лопте на шини

Слика 4.2 –Нелинеарни и линеаризовани модели лопте на шини у спрези са математичким моделом серво мотора одређеног методом сиве кутије

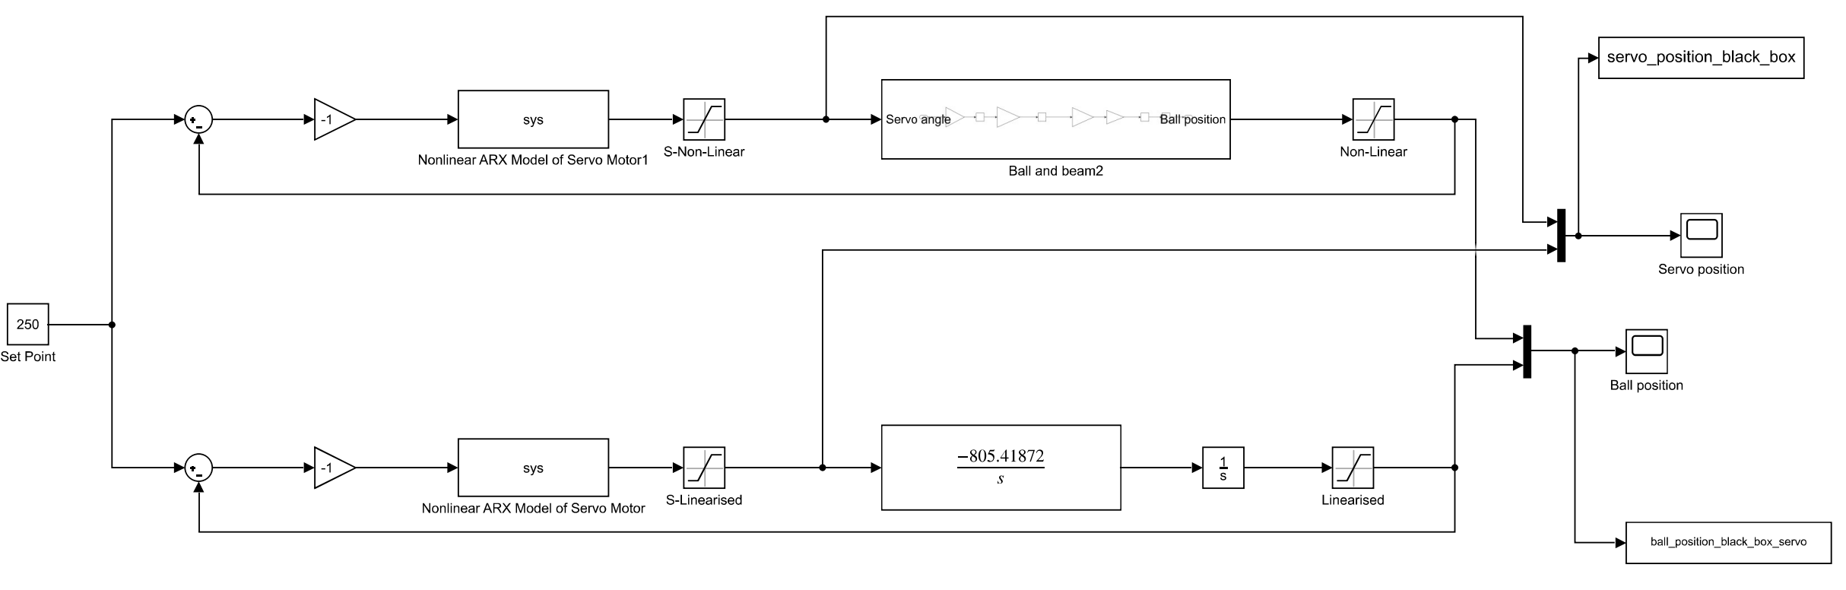
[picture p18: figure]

Слика 4.3 – Нелинеарни и линеаризовани модели лопте на шини у спрези са математичким моделом серво мотора одређеног методом црне кутије

Док су у наставку приказани одзиви система и промена угла серво мотора за различите конфигурације модела, и то следећим редоследом:

- отворени систем (слика 4.4);
- затворени систем без модела серво мотора (слика 4.5);
- затворени систем са математичким моделом серво мотора добијеним методом сиве кутије (слике 4.6 и 4.7);
- затворени систем са математичким моделом серво мотора добијеним методом црне кутије (слике 4.8 и 4.9).

Као и одзив система и промена угла серво мотора стварног система (слика 4.10).

Слика 4.4 – График одзива отворених система –

Слика 4.5 – График одзива система без серво мотора

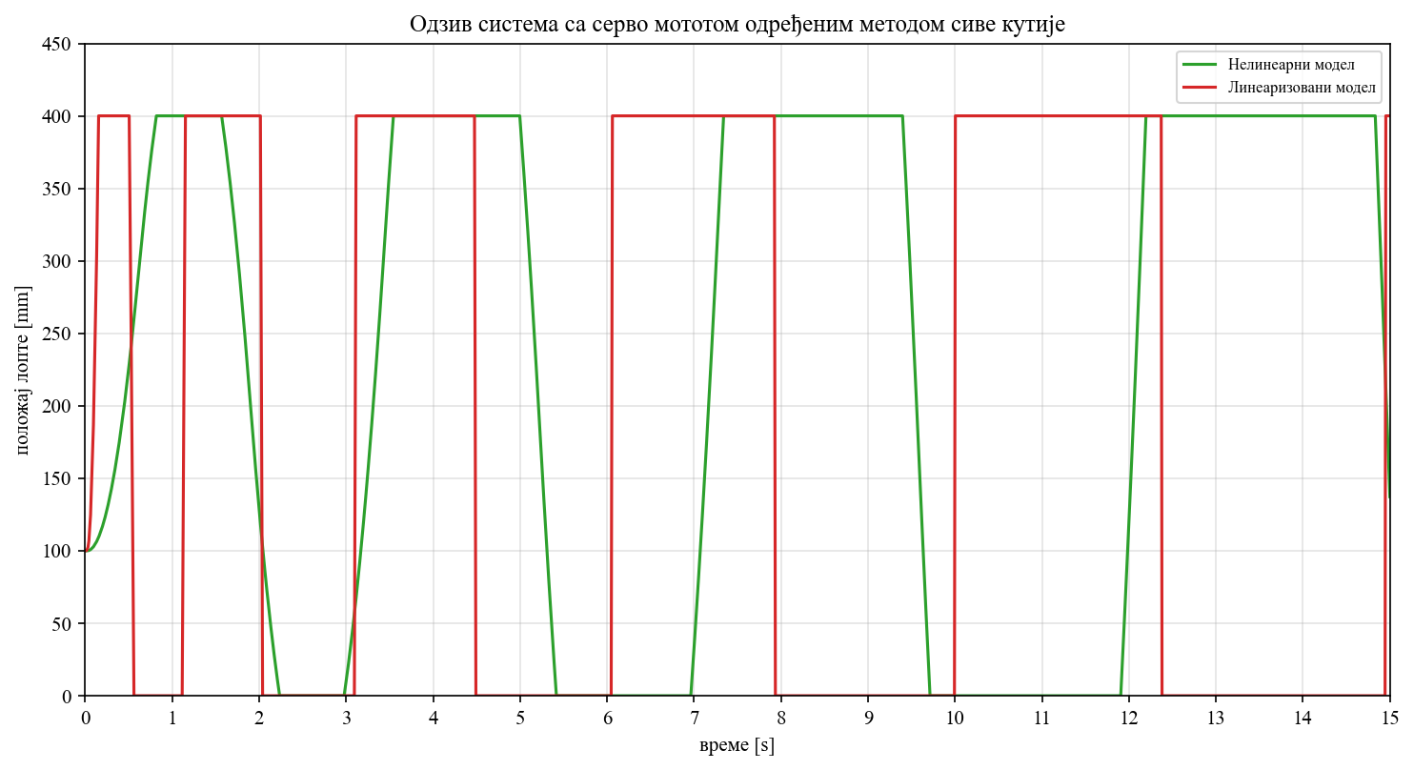
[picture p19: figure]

Слика 4.6 – График одзива система са моделом серво мотора одређеним методом сиве кутије

Слика 4.7 – График промене угла модела серво мотора одређеним методом сиве кутије

Слика 4.8 – График одзива система са моделом серво мотора одређеним методом црне кутије

Слика 4.9 – График промене угла модела серво мотора одређеним методом црне кутије

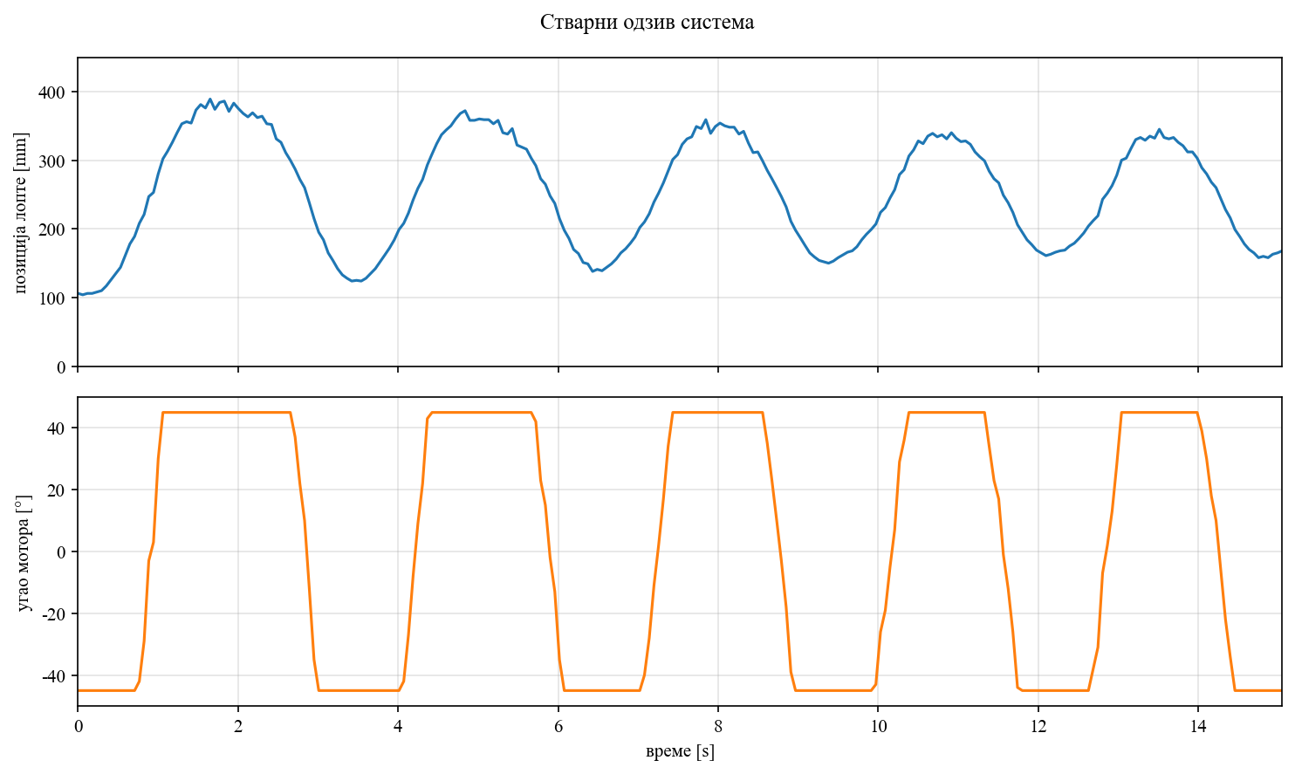
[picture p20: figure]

Слика 4.10 – Графици одзива и промене угла серво мотора стварног система

На основу анализе одзива система и промене угла серво мотора можемо закључити:

- да је систем брз:
- да нелинеарни модел даје глаткији и физички прихватљивији одзив од линеаризованог, који показује брзе, нереалистичне осцилације;
- да су одзиви система са моделом серво мотора одређеним методом сиве кутије и методом црне кутије међусобно доста слични, што се уочава на свим графицима; али је неопходно напоменути да је модел црне кутије је нешто спорији;
- да су промене угла серво мотора готово исте код сиве кутије, црне кутије и стварног система: угао се задржава на граничним вредностима ±45^(∘) ±45∘;
- да стварни одзив има мању амплитуду осцилација у односу на симулацију, док је фреквенција истог реда величине.

На основу наведеног, за даљи рад усваја се нелинеарни модел кретања лопте по шини. Док због сличног понашања оба модела серво мотора оправдано је пројектовати исти PID регулатор.

## 4.2. Одабир регулатора

Регулатор представља кључни део система аутоматског управљања. Без њега систем ради у отвореној спрези: сваки нагиб шине различит од хоризонталног равнотежног положаја ствара компоненту гравитационе силе која убрзава лопту дуж шине, па се лопта удаљава од жељене позиције. Затварањем повратне спреге регулатор непрекидно пореди измерену позицију лопте са референцом и на основу те разлике формира управљачки сигнал за серво мотор. Тиме регулатор омогућава стабилизацију нестабилног објекта, као и регулацију — задржавање лопте у близини задате позиције уз присуство поремећаја, несигурности модела и ограничења актуатора.

Избор одговарајуће структуре регулатора није ствар произвољног избора, већ треба да проистекне из особина самог система, расположивих сензора и актуатора, квалитета математичког модела и практичних ограничења имплементације. Да би се одабрала погодна структура регулатора за овај систем, потребно је одговорити на следећа питања.

1. Динамика и физика система
  - Да ли је систем линеаран или нелинеаран?

Систем је нелинеаран. Кретање лопте зависи од нагибног угла шине преко тригонометријских релација, а серво мотор је ограничен опсегом угла. На основу анализе из поглавља 4.1, за даљи рад усвојен је нелинеарни модел кретања лопте по шини; линеаризовани модел служи само као упрошћени опис, а не као основни модел за пројектовање регулатора.

- Да ли је систем отворене спреге стабилан или нестабилан?

Систем у отвореној спрези је нестабилан: при константном углу шине различитом од равнотежног положаја лопта сама од себе не мирује на жељеној позицији, већ се убрзава дуж шине. Због тога је неопходна непрекидна повратна спрега.
Затварање спреге само по себи није довољно. При испитивању затвореног система са чисто пропорционалним регулатором ( K_p =1 Kp=1) одзив је осцилаторан и не смирује се око референце.

- Да ли је систем SISO или MIMO?

По конструкцији систем је SISO: управљачка величина је жељени угао серво мотора, а мерена излазна величина је позиција лопте са ласерског сензора удаљености.

- Колико је брза динамика система?

На основу симулација из поглавља 4.1 закључено је да је систем брз. Идентификовани серво мотор се смирује реда десетине секунде, док се кретање лопте одвија на упоредивом, нешто споријем временском нивоу. Петља управљања на микроконтролеру извршава се са периодом узорковања од 50 ms, што је прихватљиво за овај механички систем.

2. Хардверска и рачунарска ограничења
  - Која су ограничења процесора?

Регулатор се имплементира на микроконтролеру Arduino Uno. Овај контролер извршава једну главну петљу, има ограничена меморијска и рачунарска средства и није погодан за сложене алгоритме са великим бројем операција у реалном времену.

- Који сензори и актуатори су на располагању?

Позиција лопте мери се ласерским сензором удаљености VL53L0X. Извршни орган је комерцијални серво мотор непознатог произвођача, који се побуђује ширинско-модулисаним сигналом. Брзина лопте се не мери директно.

- Да ли актуатор има сопствени унутрашњи регулатор?

Да. Комерцијални серво мотор већ садржи унутрашњу повратну спрегу по углу. Спољни регулатор стога задаје жељени угао, а не момент или напон, што природно води ка каскадној структури: унутрашња петља серво мотора и спољна петља која стабилизира позицију лопте.

3. Модел и познавање параметара
- Да ли постоји довољно тачан математички модел?

Да, за потребе симулационог пројектовања. На располагању је нелинеарни модел кретања лопте по шини, као и модели серво мотора добијени методом сиве и методом црне кутије. Ови модели су довољно добри за анализу затворене спреге и подешавање параметара регулатора, али нису савршени за агресивну инверзију модела или сложено нелинеарно управљање.

- Колика је очекивана варијација параметара?

Очекује се умерена варијација параметара. Она потиче од разлика у идентификованим моделима серво мотора, трења и зазора у 3D штампаној механици, заосталог нагиба шине, шума сензора и промене ефективног појачања при већим угловима. Због тога регулатор треба да буде једноставан и довољно робустан.

4. Критеријуми перформанси

Основни циљ је стабилизација система отворене спреге и регулација позиције лопте на задату референцу (у симулацијама 250 mm), уз ограничење угла серво мотора на опсег ±45^(∘) , прихватљиво пререгулисање и смиривање одзива. Детаљнији квантитативни критеријуми проверавају се симулацијом на нелинеарном моделу, а затим на стварном систему.

На основу претходне идентификације система, анализе из поглавља 4.1 и чињенице да је реч о лабораторијском („уради сам“) систему са Arduino Uno контролером, серво мотором непознатог произвођача са унутрашњим регулатором и 3D штампаном механиком, одлучује се да се пројектује PID регулатор или нека његова редукована варијанта (нпр. PD или PI). Ова фамилија регулатора одговара расположивим мерењима, рачунарским ограничењима микроконтролера и усвојеном нелинеарном моделу за пројектовање. Која ће се тачно комбинација чланова (P, I и/или D) задржати утврђује се у наставку, кроз подешавање параметара и проверу на симулацији и стварном систему.

## 4.3. Пројектовање и подешавање регулатора

Како је у претходном делу одлучено да се за управљање системом користи PID регулатор, у овом делу приступа се његовом пројектовању и подешавању параметара. Рад започиње једноставним паралелним PID регулатором. Уколико се током подешавања и испитивања покаже да овај облик није задовољавајућ, размотриће се и друге познате конфигурације PID регулатора (нпр. серијска / интерактивна форма или облик са филтрираним диференцијалним чланом).

Подешавање параметара спроводи се итеративно, поступним повећањем вредности појачања са неједнаким корацима. Након сваке пробе посматра се одзив затвореног система (и, по потреби, промена угла серво мотора), па се бира вредност која даје најповољније понашање према усвојеним критеријумима перформанси.

Неопходно је напоменути да је приликом склапања и подешавања система уочено да ласерски сензор удаљености за исту позицију лопте не даје увек исту измерену вредност, већ да очитавања осцилују у опсегу од приближно ±5mm . Да би се избегло непрекидно корекционо дејство регулатора услед ове варијације мерења када је лопта већ у близини референце, у управљање је уведена мртва зона: ако је апсолутна вредност грешке мања или једнака 5mm , сматра се да је лопта довољно близу жељене позиције и управљачки сигнал се не коригује додатно. Иста мртва зона унета је и у Simulink модел затвореног система, како би симулација верније пратила понашање стварне имплементације.

На слици 4.11 приказан је блок дијаграм комплетног затвореног система са паралелним PID регулатором, пре подешавања параметара K_p , K_i и K_d . У горњем делу приказан је систем са моделом серво мотора добијеним методом сиве кутије, а у доњем делу систем са моделом добијеним методом црне кутије. Структура регулатора, мртва зона и ограничења актуатора исте су у оба случаја; разликује се само модел серво мотора.

Слика 4.11 – Блок дијаграм затвореног система са паралелним PID регулатором: горе модел серво мотора методом сиве кутије, доле методом црне кутије

Подешавање диференцијалног појачања K_d

Подешавање је започето диференцијалним појачањем. На основу претходне анализе, задржано је K_p =−1 и K_i =0 , док је K_d мењано неравномерно инкрементално. Циљ овог корака био је да се унесе довољно пригушења како би се смањиле осцилације затвореног система.

У првој итерацији испитан је шири опсег вредности K_d . Репрезентативни одзиви приказани су на слици 4.12. Уочено је следеће:

- при малим вредностима ∣K_d ∣ (нпр. K_d =−0,05 ) систем остаје јако осцилаторан и не смирује се око референце;
- око K_d =−0,5 одзив постаје прихватљив на оба модела серво мотора;

при превеликом ∣K_d ∣ (нпр. K_d =−1,5 и K_d =−5 ) долази до погоршања, посебно код модела црне кутије, уз изражено засићење угла серво мотора.

- На основу прве итерације закључено је да се повољно подручје налази око K_d ≈−0,5 , па је у другој итерацији извршено финије подешавање у том опсегу.

Слика 4.12 – Одзив система при промени K_d ( K_p =−1 , K_i =0 ): позиција лопте и угао серво мотора

У другој итерацији K_d је мењано у ужем опсегу око −0,5 (од −0,4 до −0,8 ), и даље при K_p =−1 и K_i =0 . Одзиви су приказани на слици 4.13, а основни показатељи перформанси у табели X.X. Време смиривања T_s дефинисано је као тренутак након којег грешка остаје унутар ±10mm .

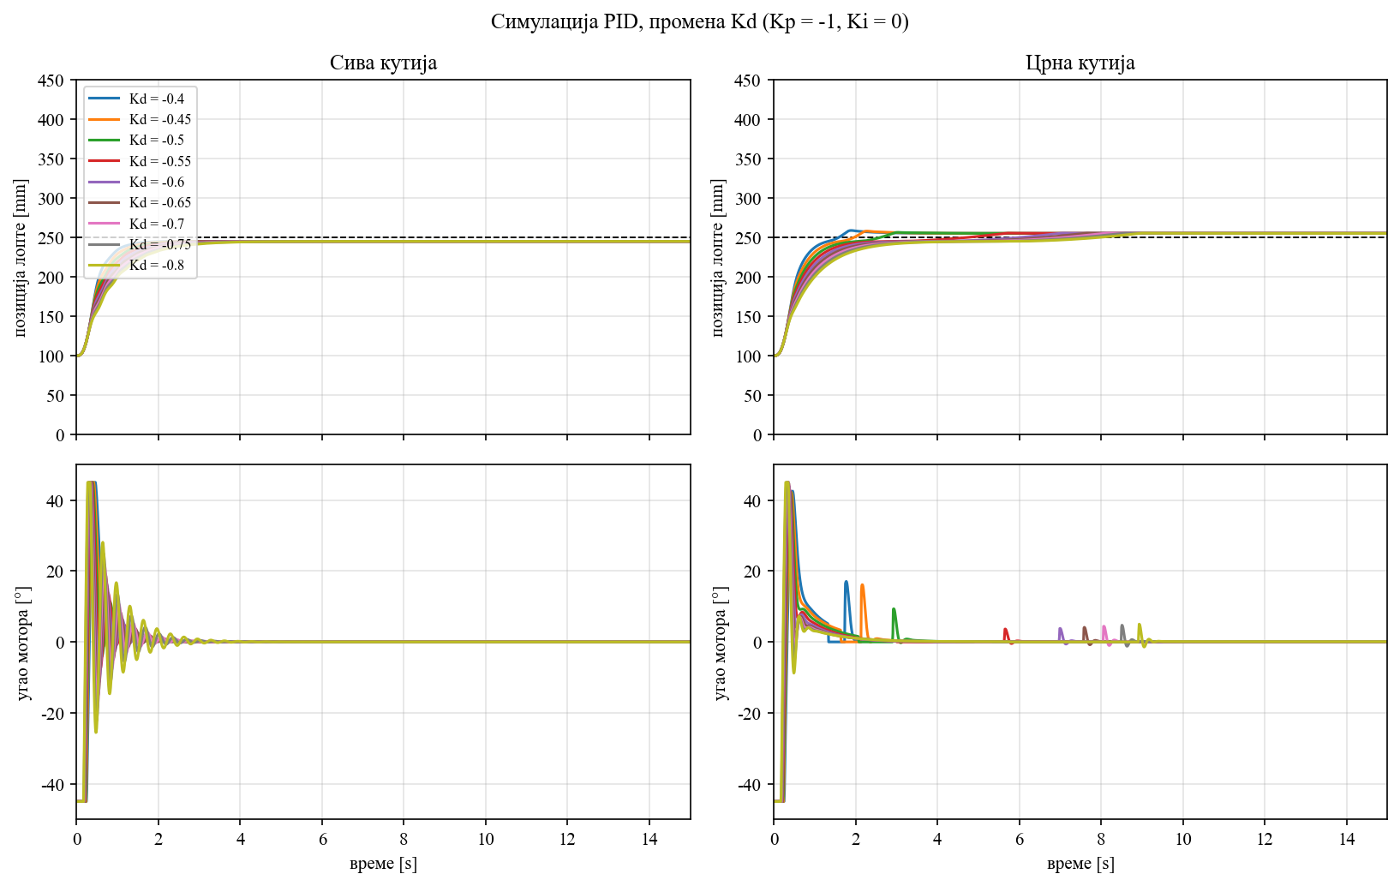
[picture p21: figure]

Слика 4.13 – Фино подешавање K_d Kd: позиција лопте и угао серво мотора (сива и црна кутија)

K_d | T_s сива [s] | T_s црна [s] | Π сива [%] | Π црна [%]
−0,4 | 1,26 | 1,08 | 0 | 1,5
−0,5 | 1,63 | 1,47 | 0 | 0,5
−0,6 | 1,99 | 1,90 | 0 | 0,1
−0,7 | 2,34 | 2,28 | 0 | 0,1
−0,8 | 2,68 | 2,63 | 0 | 0,1

Утицај K_d (друга итерација; K_p =−1 , K_i =0 ) – Табела 4.1

Све испитане вредности у овом опсегу дају стабилан одзив. Мање ∣K_d ∣ даје брже смиривање, али нешто већи прескок код модела црне кутије. Веће ∣K_d ∣ даје јаче пригушење и спорији одзив. За даљи рад усваја се: K_d =−0,7.

Ова вредност није најбржа у табели, али оставља резерву пригушења пре следећег корака — подешавања K_p . Очекивано је да повећање пропорционалног појачања убрза систем и може повећати пререгулисање, па је намерно задржано нешто јаче диференцијално дејство.

Подешавање пропорционалног појачања K_p

Након усвајања K_d =−0,7 , подешено је пропорционално појачање при K_i =0 .

У првој итерацији испитан је шири опсег K_p (слика 4.14). Уочено је:

- при премалим вредностима ∣K_p ∣ (нпр. −0,05 ) систем не достиже референцу у посматраном времену;
- око K_p =−2 добија се добар компромис брзине и пререгулисања на оба модела;
- при превеликом ∣K_p ∣ (нпр. −5 ) долази до осцилација и засићења, посебно код модела црне кутије.

Због тога је друга итерација урађена у ужем опсегу око K_p =−2 .

Слика 4.14 – Одзив система при промени K_p ( K_d =−0,7 =−0,7, K_i =0 ): позиција лопте и угао серво мотора

Резултати финијег подешавања ( K_d =−0,7 , K_i =0 ) дати су на слици 4.15 и у табели 4.2.

Слика 4.15 – Фино подешавање K_p : позиција лопте и угао серво мотора (сива и црна кутија)

K_p | T_s сива [s] | T_s црна [s] | Π сива [%] | Π црна [%]
−1,8 | 1,28 | 1,23 | 0 | 0,1
−2,0 | 1,22 | 1,04 | 0 | 0,1
−2,2 | 0,99 | 0,68 | 0,2 | 0,6
−2,4 | 0,68 | 1,35 | 0,5 | 4,8
−2,6 | 0,94 | 1,58 | 2,4 | 9,4

Утицај K_p (друга итерација; K_d =−0,7 , K_i =0 ) – Табела 4.2

Вредности око −2,0 до −2,2 дају брз одзив уз мало пререгулисање. Даљим повећањем ∣K_p ∣ пререгулисање код црне кутије нагло расте.За даљи рад усваја се: K_p =−2,2. Тиме је задржана добра брзина одзива, уз прихватљиво пререгулисање на оба модела серво мотора.

Подешавање интегралног појачања K_i

На крају је, при усвојеним K_p =−2,2 и K_d =−0,7 , испитан утицај интегралног члана. Репрезентативни одзиви приказани су на слици 4.16, а показатељи у табели 4.3.

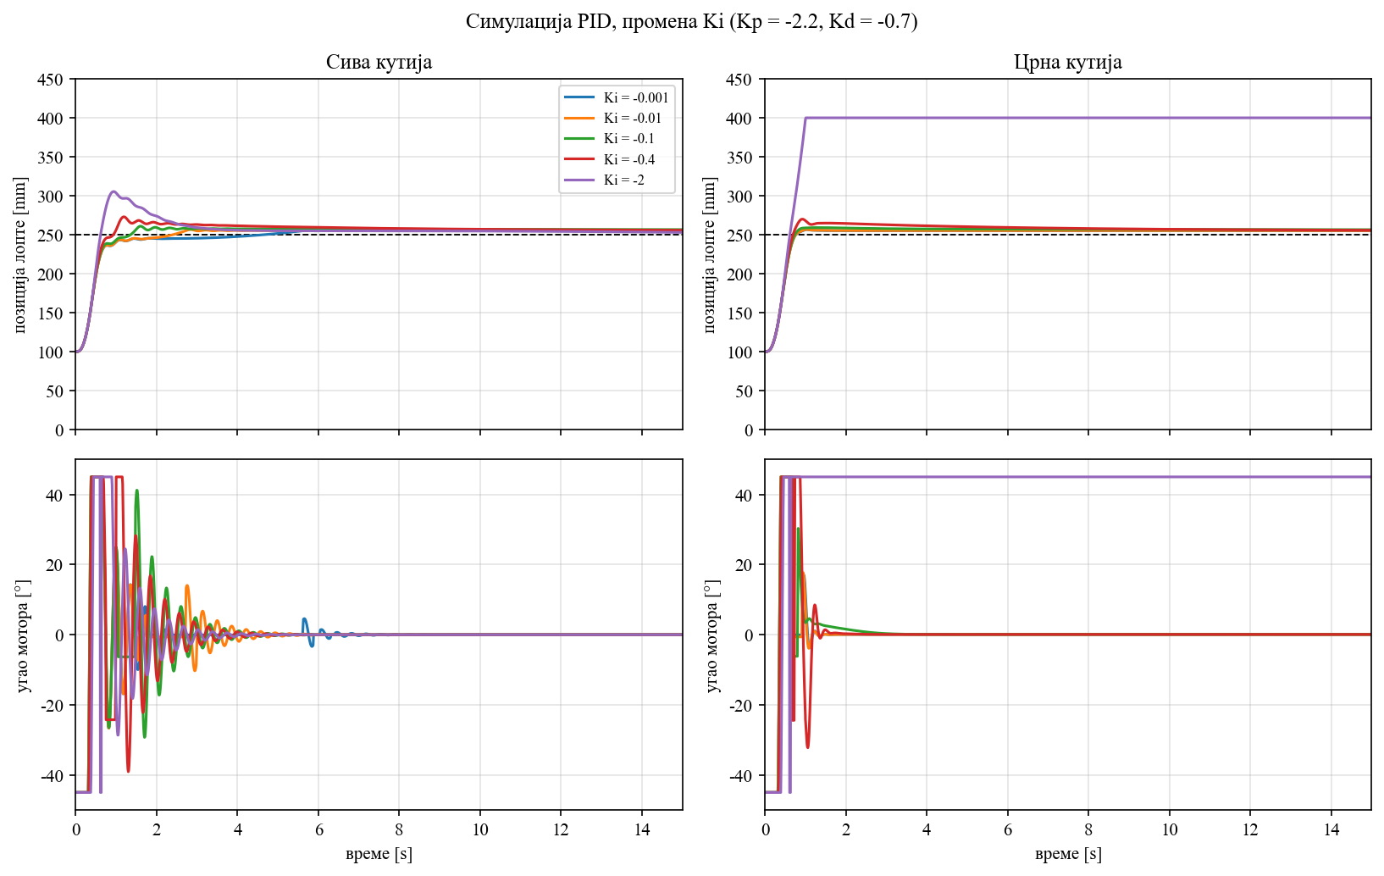
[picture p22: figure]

Слика 4.15 – Одзив система при промени K_i ( K_p =−2,2 , K_d =−0,7 ): позиција лопте и угао серво мотора

K_i | T_s сива [s] | T_s црна [s] | Π сива [%] | Π црна [%]
−0,001 | 0,99 | 0,68 | 0,2 | 0,6
−0,01 | 0,98 | 0,68 | 0,6 | 0,6
−0,1 | 1,66 | 0,67 | 1,7 | 1,0
−0,4 | 5,31 | 5,27 | 6,7 | 5,5
−2 | 2,88 | — | 20,5 | нестабилно

Утицај K_i ( K_p =−2,2 , K_d =−0,7 ) – Табела 4.3

При веома малом ∣K_i ∣ понашање је готово исто као код PD регулатора. Повећањем ∣K_i ∣ расту прескоци и време смиривања, а код већих вредности модел црне кутије постаје нестабилан. Поред тога, у систему је присутна мртва зона од ±5mm . Унутар те зоне грешка се третира као нула,па интегрални члан ионако не може значајно да уклони преосталу грешку реда величине мртве зоне. Због тога се закључује да интегрални члан у овом случају није потребан. Усваја се: K_i =0 .

На основу итеративног подешавања на нелинеарном моделу, са моделима серво мотора добијеним методом сиве и методом црне кутије, усваја се следећи регулатор:

K_p =−2,2,K_i =0,K_d =−0,7.

За управљање системом користи се једноставан паралелни PD регулатор. Овај регулатор даје задовољавајуће смиривање и регулацију око референце од 250mm 250mm, уз ограничење угла серво мотора и уз мртву зону сензора. Исти закон управљања преноси се на стварни систем (имплементација на Arduino Uno) ради експерименталне провере.

## 4.4. Имплементација регулатора

Након подешавања параметара PD регулатора у програмском пакету Simulink, исти закон управљања пренет је на стварни систем. Имплементација је урађена на микроконтролеру Arduino Uno, у наменском развојном окружењу Arduino IDE, при чему су коришћене библиотеке Servo.h за управљање серво мотором и Adafruit_VL53L0X за рад са ласерским сензором удаљености.

Основна идеја имплементације јесте затворена повратна спрега која се извршава у реалном времену. У сваком кораку главне петље микроконтролер:

- очитава тренутну позицију лопте помоћу ласерског сензора удаљености,
- израчунава грешку и вредност управљачког сигнала применом PD закона управљања,
- шаље израчунату вредност серво мотору у облику ширинско-модулисаног сигнала.

Сензор даје информацију о стварној позицији лопте, микроконтролер врши потребна израчунавања, а извршни орган прима жељени угао шине преко ширинско-модулисаног сигнала. Такође је битно напоменути да за рад:

- безбедног постављања лопте на шину пре почетка мерења,
- могућности прекида експеримента без искључивања напајања,
- једноставне контроле током испитивања и прикупљања података,

у извршни код је додата и петља којом можемо да контролишемо покретање и

заустављање система. Регулација се не покреће аутоматски, већ тек након команде G послате преко серијске комуникације, док команда S зауставља систем и враћа серво мотор у неутрални положај.

Алгоритам програма може се поделити у три целине, приказане на слици 4.16:

- Иницијализација: Покреће се серијска комуникација, серво мотор се повезује на одговарајући пин и поставља у неутрални положај, а затим се иницијализује ласерски сензор удаљености и покреће се његов континуални режим мерења.
- Провера команди: У главној петљи проверава се да ли је преко серијске комуникације стигла команда. Командом G систем прелази у режим рада, док се командом S регулација зауставља и серво мотор враћа у неутрални положај.
- Радна петљ: Када је систем активан, извршавају се следећи кораци: очитавање позиције лопте, формирање грешке, израчунавање управљачког угла применом PD закона, слање команде серво мотору, слање података на рачунар и пауза до следећег очитавања сензора.

Слика 4.16 – Алгоритам рада програма за управљање системом

Периода узроковања

У симулацијама је коришћен фиксни корак интеграције од 10ms , док је на стварном систему период главне петље 50ms . Ова разлика није узета у обзир приликом подешавања параметара регулатора у симулацији. И поред тога, стварни систем са усвојеним параметрима ради задовољавајуће.

Израчунавање управљачког сигнала и претварање у ширинско-импулсне модулације

Дискретни PD закон управљања реализован је у следећем облику:

u(k)=K_p e(k)+K_d (e(k)−e(k−1))/(Δt), e≤|5|

где су усвојена појачања K_p =−2,2 и K_d =−0,7 . Уколико је апсолутна вредност грешке мања или једнака 5mm , активира се мртва зона, при чему је излаз регулатора једнак нули, а претходна вредност грешке се ресетује. Излаз регулатора представља жељени угао шине и ограничен је на опсег ±45^(∘) , чиме је у имплементацији поновљено засићење актуатора усвојено у симулационом моделу.

Добијени угао се затим линеарно пресликава у трајање импулса ширинско-модулисаног сигнала према изразу:

PWM=500+(α+135)/270⋅2000[μs],

што одговара радном опсегу коришћеног серво мотора, односно трајању импулса од 500 до 2500μs за угао од −135^(∘) до 135^(∘) (неутрална позиција 180°).

Негативан предзнак појачања K_p и K_d последица је оријентације сензора и смера дејства серво мотора у конкретном склопу, а не другачијег облика регулатора у односу на симулациони модел.

Слање података преко серијске комуникације

Током рада микроконтролер шаље податке у формату време [ms], позиција лопте [mm], угао серво мотора [°], што омогућава касније поређење експерименталног одзива са резултатима симулације. Ова операција се извршава након сваког корака регулације и незнатно продужава трајање главне петље, али не мења структуру алгоритма нити битно утиче на понашање система.

Комплетан програм за управљање системом за балансирање лопте на шини дат је у наставку. Програм обухвата дефиниције параметара, иницијализацију хардвера, реализацију регулатора са мртвом зоном, претварање угла у ширинско-модулисани сигнал, као и логику за покретање и заустављање система преко серијскe комуникације.

Током имплементације и тестирања на реалном систему параметри регулатора су незнатно кориговани у односу на вредности добијене у фази пројектовања: пропорционално појачање је снижено на K_p =−1, а уведено је и мало интегрално дејство K_i =−0,01 . Разлози за ове измене и анализа понашања реалног система приказани су у наредном поглављу.

#include <Servo.h>

#include "Adafruit_VL53L0X.h"

const int SERVO_PIN = 5;

const int ZERO_PWM = map(0, -135, 135, 500, 2500);

const float BEAM_MIN = -45.0f;

const float BEAM_MAX = 45.0f;

Servo beamServo;

Adafruit_VL53L0X lox;

const float SETPOINT_MM = 250.0f;

const float TOLERANCE_MM = 5.0f;

const unsigned long LOOP_MS = 50;

float Kp = -1.2f;

float Ki = -0.01f;

float Kd = -0.7f;

bool running = false;

float distance_mm = 0.0f;

float beam_deg = 0.0f;

float integral = 0.0f;

float prev_error = 0.0f;

unsigned long t0_ms = 0;

void setBeamAngle(float angle_deg) {

float pwm_f = 500.0f + (angle_deg + 135.0f) * (2000.0f / 270.0f);

int pwm = (int)lround(pwm_f);

beamServo.writeMicroseconds(pwm);

}

void holdNeutral() {

beam_deg = 0.0f;

beamServo.writeMicroseconds(ZERO_PWM);

}

void readDistance() {

if (!lox.isRangeComplete()) {

return;

}

uint16_t raw = lox.readRange();

if (raw != 65535) {

distance_mm = (float)raw;

}

}

float pidStep(float error) {

if (fabs(error) <= TOLERANCE_MM) {

integral = 0.0f;

prev_error = 0.0f;

return 0.0f;

}

const float dt = LOOP_MS / 1000.0f;

integral += error * dt;

float D = Kd * (error - prev_error) / dt;

prev_error = error;

beam_deg = constrain(Kp * error + Ki * integral + D, BEAM_MIN, BEAM_MAX);

return beam_deg;

}

void logData() {

Serial.print(millis() - t0_ms);

Serial.print(',');

Serial.print((int)lround(distance_mm));

Serial.print(',');

Serial.println(beam_deg, 2);

}

void setup() {

Serial.begin(115200);

while (!Serial) {

delay(1);

}

beamServo.attach(5);

holdNeutral();

if (!lox.begin()) {

Serial.println(F("VL53L0X init failed"));

while (1) {

delay(100);

}

}

lox.startRangeContinuous();

Serial.println(F("Ball and Beam v1"));

Serial.println(F("G = start, S = stop"));

Serial.println(F("time_ms,distance_mm,beam_deg"));

}

void loop() {

if (Serial.available()) {

char cmd = Serial.read();

while (Serial.available()) {

Serial.read();

}

if (cmd == 'G' || cmd == 'g') {

running = true;

t0_ms = millis();

integral = 0.0f;

prev_error = 0.0f;

holdNeutral();

Serial.println(F("RUN"));

} else if (cmd == 'S' || cmd == 's') {

running = false;

holdNeutral();

Serial.println(F("STOP"));

}

}

if (!running) {

return;

}

readDistance();

float error = SETPOINT_MM - distance_mm;

setBeamAngle(pidStep(error));

logData();

delay(LOOP_MS);

}

## 4.5. Поређење математичких модела са стварним системом

Пре самог упоређивања математичког модела са стварним спроведено је десет узастопних експеримената под истим условима на основу којих је урађена анализа и уочено следеће:

- Прелазни режим је изразито понављив. Лопта долази у околину референтне вредности за 2,6±0,8s , уз прескок од 12 до 19mm у зависности од стране са које полази, што показује да је одзив приближно симетричан.
- У устаљеном стању лопта не мирује, већ се одржава ситно таласање око референце са стандардном девијацијом од 7,9mm . Лопта се налази унутар зоне од ±5mm у 40% времена, а унутар зоне од ±20mm у око 90% времена.
- Стварни период одабирања износи 59ms уместо номиналних 50ms , а стандардна девијација шума мерења положаја износи приближно 3mm , при чему расте са растојањем: од 1,8mm на блиским растојањима до 5,8mm преко 350mm .
- Јавља се статичка грешка: лопта се у просеку не смирује на референтној позицији, већ 7,0mm даље од ње, при чему се појединачни експерименти крећу у распону од −5,3 до +24,4mm .

Слика 4.17 – Стварни одзив система (десет експеримената)

Да би поређење са мерењима било смислено, Simulink модел је најпре ажуриран (слика 4.18) параметрима регулатора коришћеним на реалном систему. Такође поред је измењен и начин на који је регулатор реализован у моделу. Уместо континуалног регулатора, у повратну спрегу је уведено коло задршке нултог реда са периодом одабирања од 59ms , диференцијално дејство реализовано је дискретним блоком, а интегрално дејство дискретним интегратором.

Слика 4.18 – Финални Simulink модел

За проверу верности модела изабрана су четири насумична експеримента — два са горње и два са доње стране шине — са почетним положајима r_0 ∈{380, 379, 71, 70}mm . За сваки експеримент изведена је симулација са истим почетним условом, посебно за модел са серво мотором одређеним методом сиве кутије и посебно за модел са серво мотором одређеним методом црне кутије. Динамика лопте, регулатор, мртва зона и период одабирања идентични су у обе симулације; једина разлика је модел серво мотора. Тиме се поређење своди на питање који од два модела боље репродукује понашање реалног система у затвореној спрези.

Степен преклапања изражен је у процентима као:

100(1−(∥y−^y)/(∥y−ˉy)),

где је y измерени положај лопте, ^y одзив симулације, а ˉy средња вредност мерења. Вредност од 100% означава потпуно преклапање, док вредност близу нуле значи да модел није бољи од пуког предвиђања средње вредности.

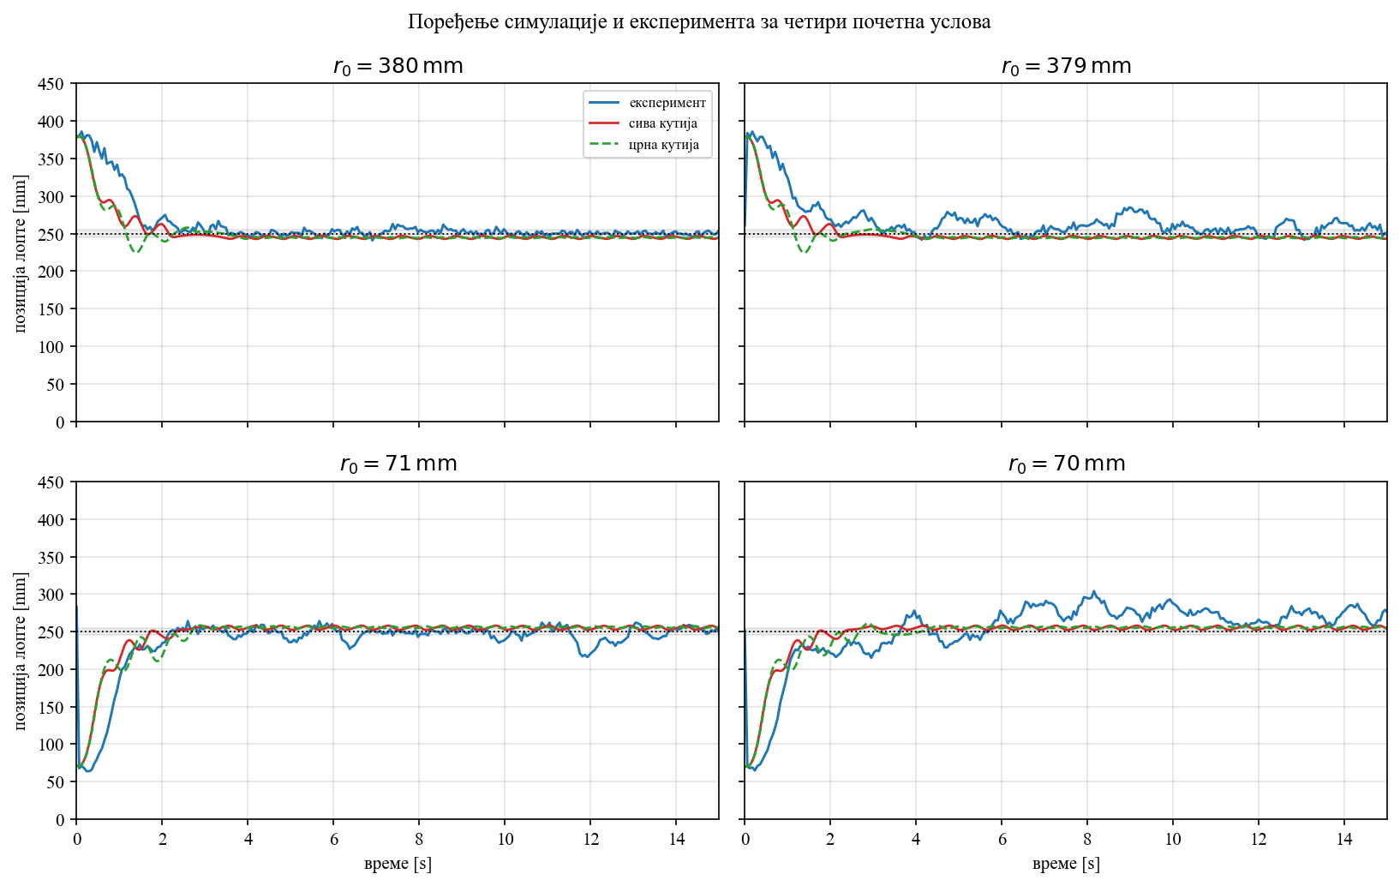
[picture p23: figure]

Слика 4.19 – Поређење симулације и експеримента за четири почетна услова

На основу слике и израчунатог преклапања уочава се следећ:

- Оба модела дају стабилан одзив и прате смер кретања лопте у свим четири случајевима. Просечно преклапање на целој трајекторији износи 35,5% за модел сиве кутије и 31,5% за модел црне кутије. У прелазном режиму ( 0 – 4s ) разлике су израженије: 32,6% наспрам 27,0% . Модел сиве кутије, дакле, нешто боље преклапа мерење, али разлика није велика.
- При поласку одозго ( r_0 =380mm и r_0 =379mm ) оба модела су бржа од експеримента: у зону од ±10mm улазе за око 2s , док експеримент за то треба 3,4s у најбољем случају. Преклапање је највеће код експеримента са r_0 =380mm ( 45% сива кутија, 36% црна кутија). Код r_0 =379mm преклапање пада ( 16% односно 11% ), јер експеримент у устаљеном стању показује израженије осциловање и статичку грешку које симулација не репродукује.
- При поласку одоздо ( r_0 =71mm и r_0 =70mm ) модели су међусобно скоро изједначени, са преклапањем од око 40% . Модел црне кутије овде достиже зону ±10mm приближно у исто време као експеримент ( ≈2,6s ), док је модел сиве кутије и даље бржи ( ≈1,6s ).

Ни један модел не репродукује статичку грешку реалног система. У симулацији се лопта зауставља на ивици мртве зоне (око 245mm ), док на поставци средња вредност често лежи изнад референце. Разлог је што модел не садржи механички нагиб нултог положаја греде. Осциловање у устаљеном стању на реалном систему такође је веће него у симулацији, јер симулација не садржи шум мерења који се на поставци појачава диференцијалним дејством.

Поређење у затвореној спрези показује да модел са серво мотором одређеним методом сиве кутије нешто верније репродукује понашање управљаног система од модела одређеног методом црне кутије, при истим параметрима регулатора и истим почетним условима. Разлика у преклапању је умерена. Модел црне кутије и даље даје стабилан и употребљив одзив, посебно при поласку одоздо, али за пројектовање регулатора поузданији опис постројења пружа модел сиве кутије.

# 5. Закључак

Циљ овог мастер рада био је пројектовање и израда система за балансирање лопте на шини, одређивање његовог математичког модела — са посебним акцентом на идентификацију серво мотора методом црне кутије — као и пројектовање, имплементација и испитивање регулатора на реалној поставци.

У првом делу рада систем је пројектован и израђен. Изабрана је конфигурација са непокретним ослонцем на једном крају шине и погоном преко система полуга на другом. Положај лопте мерен је ласерским сензором растојања, као извршни орган коришћен је серво мотор, а управљање је реализовано на микроконтролеру Arduino Uno. Нестандардни делови израђени су адитивном технологијом, а систем је склопљен и ожичен у складу са пројектованом шемом.

У другом делу одређен је математички модел система. Динамика лопте на шини описана је на основу закона механике. За серво мотор, чија унутрашња структура није у потпуности позната, спроведена је идентификација на основу експериментално прикупљених улазно-излазних података. Модел је одређен на два начина: методом сиве кутије, полазећи од општег модела електромотора једносмерне струје са редуктором и естимацијом параметара преносне функције, и методом црне кутије, применом неуронске мреже / NARX структуре. Оба модела валидирана су на независном скупу података и уграђена у Simulink окружење, заједно са нелинеарним моделом кретања лопте.

У трећем делу пројектован је и имплементиран регулатор. На основу карактеристика објекта, ограничења хардвера и захтева квалитета регулације усвојен је PID регулатор. Параметри су подешени итеративно у симулацији, а затим пренети на микроконтролер. При имплементацији уведена је мртва зона ради смањења утицаја шума мерења у близини референце, а током испитивања на реалном систему додато је интегрално дејство и кориговано пропорционално појачање. Регулатор успешно стабилизује лопту око жељене позиције од 250mm .

На крају је извршено поређење симулације и експеримента за четири почетна услова. Оба модела серво мотора дају стабилан одзив и прате смер кретања лопте. Просечно преклапање са мерењем износи око 35,5% за модел одређен методом сиве кутије и око 31,5% за модел одређен методом црне кутије. Модел сиве кутије стога нешто верније описује понашање управљаног система у затвореној спрези, док модел црне кутије остаје употребљив и даје блиске резултате, посебно при поласку лопте са доње стране шине. Разлике између симулације и експеримента — бржи одзив модела, одсуство статичке грешке и слабије осциловање у устаљеном стању — последица су тога што модел кретања лопте по шини није потпун и што у њега нису урачунати разни физички фактори и несавршености реалног система.

На основу свега изнетог може се закључити да је циљ рада остварен: израђен је функционалан систем за балансирање лопте на шини, идентификовани су модели серво мотора методама сиве и црне кутије, пројектован и имплементиран је регулатор који стабилно управља системом, а валидацијом у затвореној спрези показано је да оба модела могу да се користе за анализу и пројектовање, уз благу предност модела сиве кутије у погледу преклапања са мерењем на реалној поставци.

# 6. Додатак

## 6.1. Додатак А – Техничка документација стандардних компоненти

### 6.1.1. Микроконтролер – Arduino Uno

У данашње време је немогуће замислити аутоматски систем без присуства неког типа рачунара. Рачунарске јединице попут PLC-а се данас користе у различитим индустријама где је потребно управљати робусним стварима попут производних линија и котловима за прављење полуфабриката од различитих метала, док се рачунари попут микроконтролера и микропроцесора користе у авионима, аутомобилима, али и многим другим индустријама за обраду сигнала и фино управљање актуатора.

У системима аутоматског управљања рачунари на улаз добијају сигнал жељеног динамичког понашања система (мада то често може бити и записано у његовој меморији), као и мерени одзив система, односно стварно динамичко понашање система. На основу ових улазних величина и одговарајућег алгоритма управљања он израчунава вредност управљања.

За потребе овог система изабрана је Arduino Uno (слика 2.3) развојна плоча са Atmel-овим микроконтролером. Arduino Uno је платформа отвореног кода коју је развио Arduino тим. Ова платформа се састоји од хардверског и софтверског дела, а користи се за стварање и контролисање интерактивних електронских пројеката.

Техничке карактеристике и шема улазно/излазних пинова овог микроконтролера су приказани у табели 7.1 и слици 7.1.

Слика 6.1 – Arduino Uno

Микроконтролер | ATmega328P
Радни напон | 5 V
Улатни напон | 7-12 V
Дигитални У/И пинови | 14
PWM дигитални У/И пинови | 6
Аналогни улазни пинови | 6
Једносмерна струја по У/И пину | 20 mA
Флеш меморија | 32 KB (ATmega328P)
SRAM | 2 KB (ATmega328P)
EEPROM | 1 KB (ATmega328P)
Радни такт | 16 MHz
Дужина | 68.6 mm
Ширина | 53.4 mm
Маса | 25 g

Техничке карактеристике микроконтролера Arduino Uno – Табела 6.1

Слика 6.2 – Шема улазно/излазних пинова –

### 6.1.2. Сензор растојања – VL53L0X

VL53L0X је сензор за мерење растојања заснован на Time-of-Flight (ToF) технологији. Сензор користи инфрацрвени VCSEL емитер таласне дужине 940 nm и SPAD пријемну матрицу за детекцију одбијеног сигнала. На основу времена проласка светлосног сигнала до објекта и назад, интерна електроника сензора одређује растојање. Сензор омогућава мерење апсолутног растојања до 2 m. Принцип рада сензора може се описати кроз следеће кораке:

1. Емитовање сигнала: Сензор емитује кратке импулсе инфрацрвеног зрачења помоћу VCSEL емитера.
2. Одбијање сигнала: Емитовано зрачење се одбија од површине објекта.
3. Пријем сигнала: SPAD пријемна матрица региструје повратни сигнал.
4. Израчунавање растојања: Уграђена електроника одређује време проласка сигнала и на основу њега израчунава растојање до објекта.

Комуникација са микроконтролером остварује се путем I²C интерфејса, док се сигнал GPIO1 може користити за генерисање прекида након завршетка мерења. Сензор такође поседује XSHUT улаз који се користи за ресетовање и искључивање сензора.

За потребе овог система коришћен је High Accuracy режим мерења, са временским буџетом од 200 ms, чиме је приоритет дат стабилности и прецизности мерења растојања.

Техничке карактеристике VL53L0X сензора приказане су у табели 7.2.

Слика 6.3 – Сензор растојања VL53L0X

Техничка карактеристика | Вредност
Тип сензора | Time-of-Flight (ToF)
Инфрацрвени емитер | VCSEL, 940 nm
Максимално растојање | до 2 m
Радни напон | 2,6 – 3,5 V
Радна температура | −20 °C до 70 °C
Комуникациони интерфејс | I²C
Димензије сензора | 4,4 × 2,4 × 1,0 mm
Временски буџет мерења | 200 ms

Техничке карактеристике сензора VL53L0X – Табела 6.2

### 6.1.3. Серво мотор

Серво мотори једносмерне струје су специјализовани типови електромотора дизајнирани за прецизну контролу угла или линеарне позиције, брзине и убрзања. Широко се користе у апликацијама где је прецизна контрола кретања критична, као што су роботи, CNC машине и аутоматизациони системи.

За овај пројекат изабран је серво мотор непознатог произвођача, који је широко коришћен модел, погодан за различите апликације, укључујући хоби роботику, возила на даљинско управљање (RC) и основне задатке аутоматизације. Пружа добар баланс између перформанси и цене, чинећи га популарним избором како за почетнике тако и за искусне програмере. Техничке карактеристике овог мотора можете наћи у табели 7.3.

Тип мотора | Стандардни серво мотор једносмерне струје
Радни напон | 6V до 8.3V
Стални обртни момент | 6V: 58 kg.cm, 8.3V: 70 kg.cm
Радна брзина | 6V: 0.17 сек/60°, 8.3V: 0.13 сек/60°
Тип зупчаника | Метални зупчаници
Контролни систем | PWM (Ширина импулса модулација)
Опсег ширине импулса | 500-2500 µs
Опсег ротације | 270°
Тежина | 158g
Димензије | 40.7mm x 19.7mm x 42.9mm
Тип конектора | тропински JR
Тип лежаја | Једноредни куглични лежај
Температурни опсег | -15°C до +70°C
Материјал кућишта | Алуминијум

Техничке карактеристике серво мотора – Табела 6.3

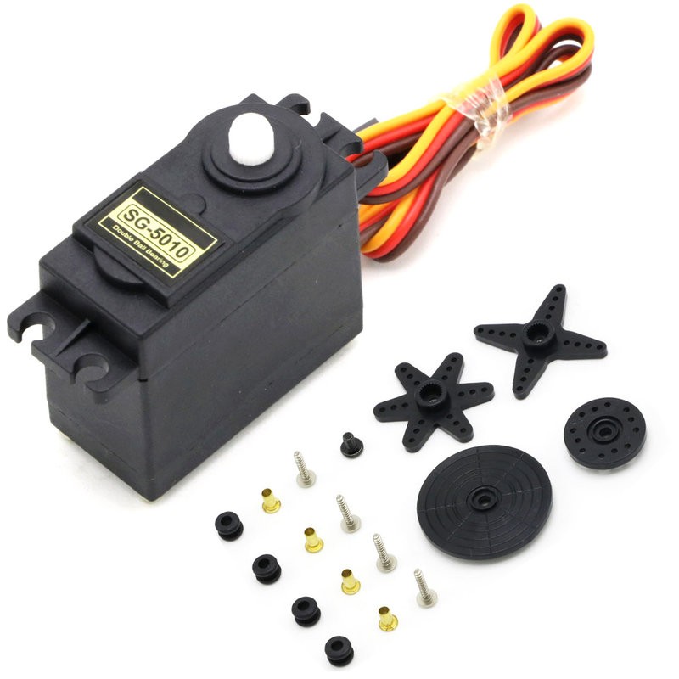
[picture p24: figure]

Слика 6.4 – Серво мотора

### 6.1.4. Микропроцесор - Raspberry Pi 4

Raspberry Pi 4 је моћна и свестрана развојна плоча са микропроцесором, дизајнирана за широк спектар апликација, од образовања до напредних уграђених система. Са својим четворојезгарним ARM Cortex -А72 процесором, вишеструким опцијама меморије и обимним могућностима повезивања, Raspberry Pi обезбеђује процесорску снагу и флексибилност неопходну за једноставне прототипе, као и за сложене уграђене пројекте. Подржава два 4К дисплеја, брзе USB 3.0 везе и има робусне могућности умрежавања, што га чини идеалним за мултимедијалне апликације, IoT уређаје и много више. Било да развијате хоби пројекат малог обима или индустријску апликацију у пуном обиму, Raspberry Pi је поуздана и богата функцијама платформа.Техничке карактеристике овог сензора се могу пронаћи у табели 7.4.

Слика 6.5 – Raspberry Pi 4 и шема улазно/излазних пинова –

Процесор | Broadcom BCM2711, Quad-core Cortex-A72 (ARM v8) 64-bit, 1.5 GHz
Графичка карта | VideoCore VI, подржава OpenGL ES 3.0, Vulkan, H.265 (4Kp60 декодирање)
Меморија (RAM) | 8GB LPDDR4 SDRAM
Меморија за складиштење | MicroSD картица (подржава велике брзине UHS-I), USB boot support
Мрежа | Gigabit Ethernet, Dual-band 802.11ac Wi-Fi, Bluetooth 5.0
USB портови | 2x USB 3.0, 2x USB 2.0
Видео излаз | 2x Micro-HDMI (подржава резолуцију до 4Kp60)
Аудио излаз | четворо полни стерео излаз и композитни видео, HDMI аудио, I²S аудио
Улазно/Излазни Пинови | 40 пинова, 3.3V логика
Интерфејс за камеру | MIPI CSI
Интерфејс за дисплеј | MIPI DSI (Display Serial Interface)
Напајање | 5V/3A преко USB-C конектора
Оперативни системи | Raspberry Pi OS, Ubuntu, Manjaro, LibreELEC, RetroPie
Димензије | 85.6mm x 56.5mm x 17mm
Маса | 46g
Типови комуникације | 2x UART, 2x SPI, 5x I²C, 27x GPIO, 1x PCM/I²S, 1x SDIO
Потрошња енергије | У стању мировања 2.7W, приликом максималног оптерећења 7W

Техничке карактеристике микропроцесора Raspberry Pi 4 – Табела 6.4

### 6.1.5. Ротациони енкодер – LDP3806–600BM–5G –24C

Ротациони енкодер је електромеханички уређај који конвертује угаону позицију или кретање осовине у аналогни или дигитални сигнал. Ови сигнали су кључни за одређивање позиције, брзине и правца ротационог кретања. Ротациони енкодери се широко користе у апликацијама које захтевају прецизну контролу ротационог кретања, као што су системи за контролу мотора, роботика, CNC машине и индустријска аутоматизација.

LDP3806-600BM-G5-24C је инкрементални ротациони енкодер познат по својој високој резолуцији и робусном дизајну, што га чини погодним за апликације које захтевају прецизну контролу кретања. Идеалан је за примене које захтевају повратне информације високе резолуције у изазовним окружењима, као што су прецизна контрола мотора, роботика и индустријска аутоматизација. Његова робусна конструкција обезбеђује поуздан рад у захтевним условима.

Тип енкодера | Инкрементални ротациони енкодер
Резолуција | 600 импулса по револуцији
Пречник осовине | 6mm
Радни напон | 5V до 24V DC
Тип излаза | Квадратни (А и Б фаза сигнали)
Излазни напон | Високо: ≥2.4V (TTL-компатибилан), Ниско: ≤0.4V
Максимална фреквенција одговора | 100 kHz
Максимална брзина ротације | 5000 ротација у минути
Излазна струја | 30 mA макс по каналу
Радна температура | -10°C до +70°C
Конекција | Кабл са штитом, 5-пински конектор
Димензије | Пречник 38mm x дужина 44mm
Тежина | 150g

Техничке карактеристике ротационог енкодера LDP3806-600BM-G5-24C – Табела 6.5

Слика 6.6 – Ротационог енкодера LDP3806-600BM-G5-24C –

## 6.2. Додатак Б – Помоћне скрипте
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

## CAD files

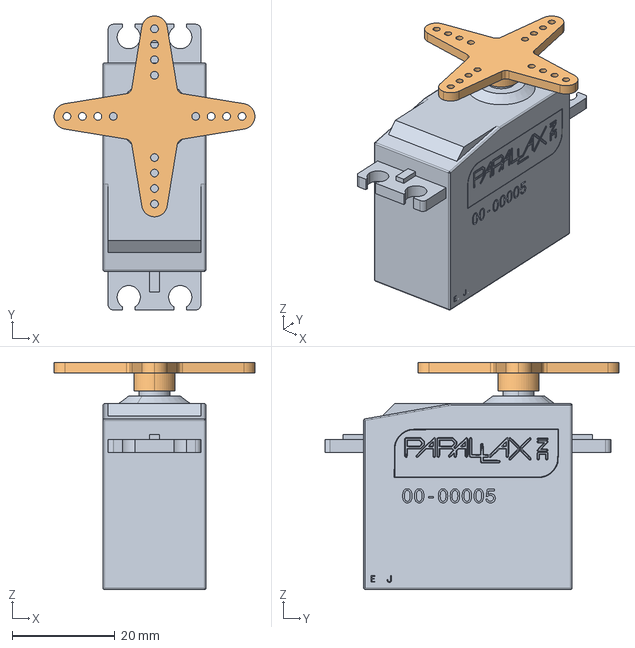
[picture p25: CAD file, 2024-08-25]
Ball_and_Beam_CAD_model/Ostali delovi/Gotovi modeli/Parallax Servo 900-00005.stp
39.0 x 57.1 x 44.1 mm

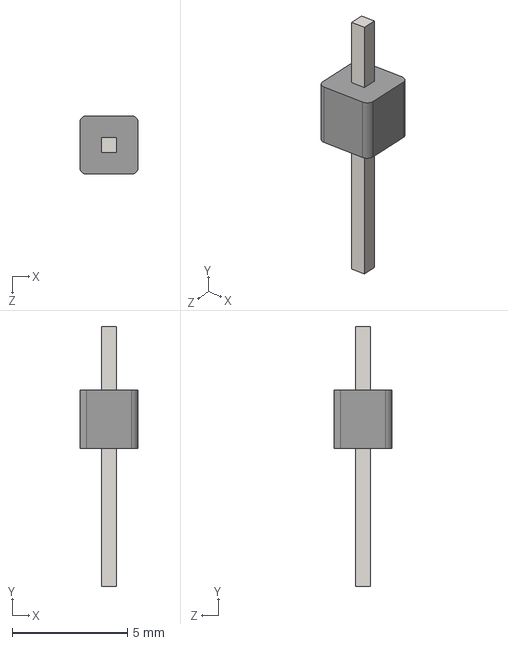
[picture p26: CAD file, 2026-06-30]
Ball_and_Beam_CAD_model/Ostali delovi/Gotovi modeli/VL53L0X/STEP/headerPin.STEP
2.54 x 11.3 x 2.54 mm

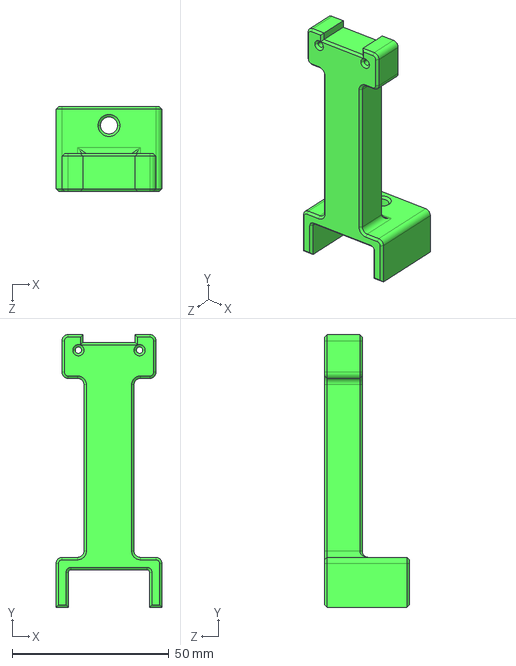
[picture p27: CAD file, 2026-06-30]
Ball_and_Beam_CAD_model/Ostali delovi/Gotovi modeli/VL53L0X/STEP/bracket.STEP
33.8 x 87.0 x 27.0 mm

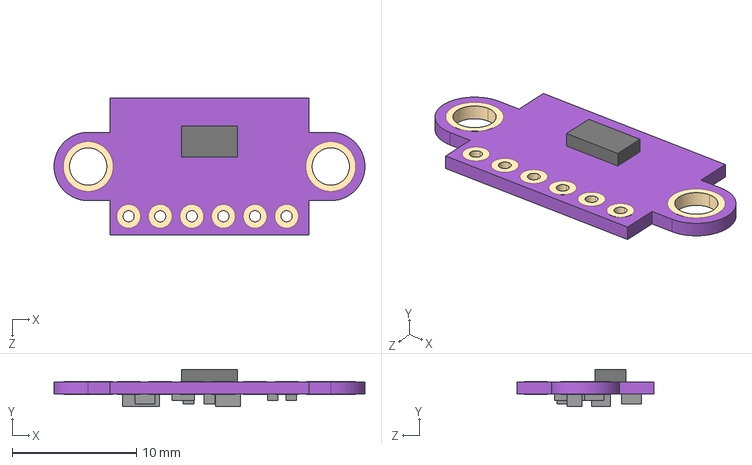
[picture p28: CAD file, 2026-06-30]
Ball_and_Beam_CAD_model/Ostali delovi/Gotovi modeli/VL53L0X/STEP/sensor.STEP
25.0 x 3.00 x 11.0 mm

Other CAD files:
Ball_and_Beam_CAD_model/Ostali delovi/Gotovi modeli/VL53L0X/STEP/sensor_assy.STEP
Ball_and_Beam_CAD_model/Balanser Ping Pong Lopte.CATProduct
Ball_and_Beam_CAD_model/Guide.CATPart
Ball_and_Beam_CAD_model/ISO 4032 NUT M4 STEEL GRADE A HEXAGON.2.CATPart
Ball_and_Beam_CAD_model/ISO 4032 NUT M4 STEEL GRADE A HEXAGON.3.CATPart
Ball_and_Beam_CAD_model/ISO_2009_M3x10_STEEL_GRADE_A_COUNTERSUNK_SLOTTED_FLAT_HEAD_SCREW.CATPart
Ball_and_Beam_CAD_model/ISO_2009_M4x10_STEEL_GRADE_A_COUNTERSUNK_SLOTTED_FLAT_HEAD_SCREW.CATPart
Ball_and_Beam_CAD_model/ISO_2009_M4x12_STEEL_GRADE_A_COUNTERSUNK_SLOTTED_FLAT_HEAD_SCREW.CATPart
Ball_and_Beam_CAD_model/ISO_2009_M4x14_STEEL_GRADE_A_COUNTERSUNK_SLOTTED_FLAT_HEAD_SCREW.CATPart
Ball_and_Beam_CAD_model/ISO_4032_M3_STEEL_GRADE_A_HEXAGON_NUT.CATPart
Ball_and_Beam_CAD_model/ISO_4032_M4_STEEL_GRADE_A_HEXAGON_NUT.CATPart
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

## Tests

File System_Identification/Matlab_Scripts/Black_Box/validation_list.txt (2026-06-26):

../../Data/Encoder_data/Test_2/Test_30/Processed/Test_0.csv
../../Data/Encoder_data/Test_2/Test_30/Processed/Test_3.csv
../../Data/Encoder_data/Test_2/Test_30/Processed/Test_7.csv
../../Data/Encoder_data/Test_2/Test_30/Processed/Test_8.csv
../../Data/Encoder_data/Test_2/Test_45/Processed/Test_6.csv
../../Data/Encoder_data/Test_2/Test_45/Processed/Test_9.csv
../../Data/Encoder_data/Test_2/Test_45/Processed/Test_11.csv

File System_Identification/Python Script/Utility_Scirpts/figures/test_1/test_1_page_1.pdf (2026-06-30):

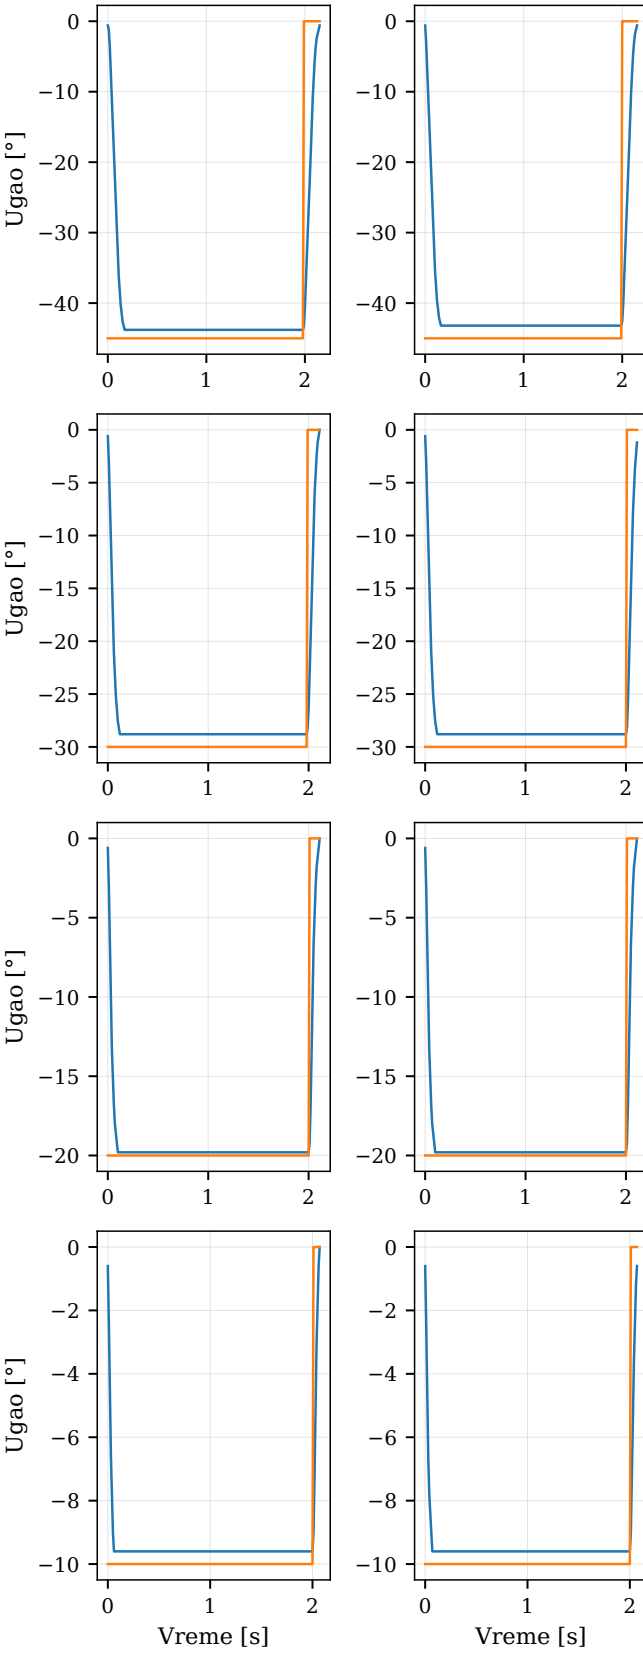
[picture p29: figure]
Ugao [°]; Vreme [s]
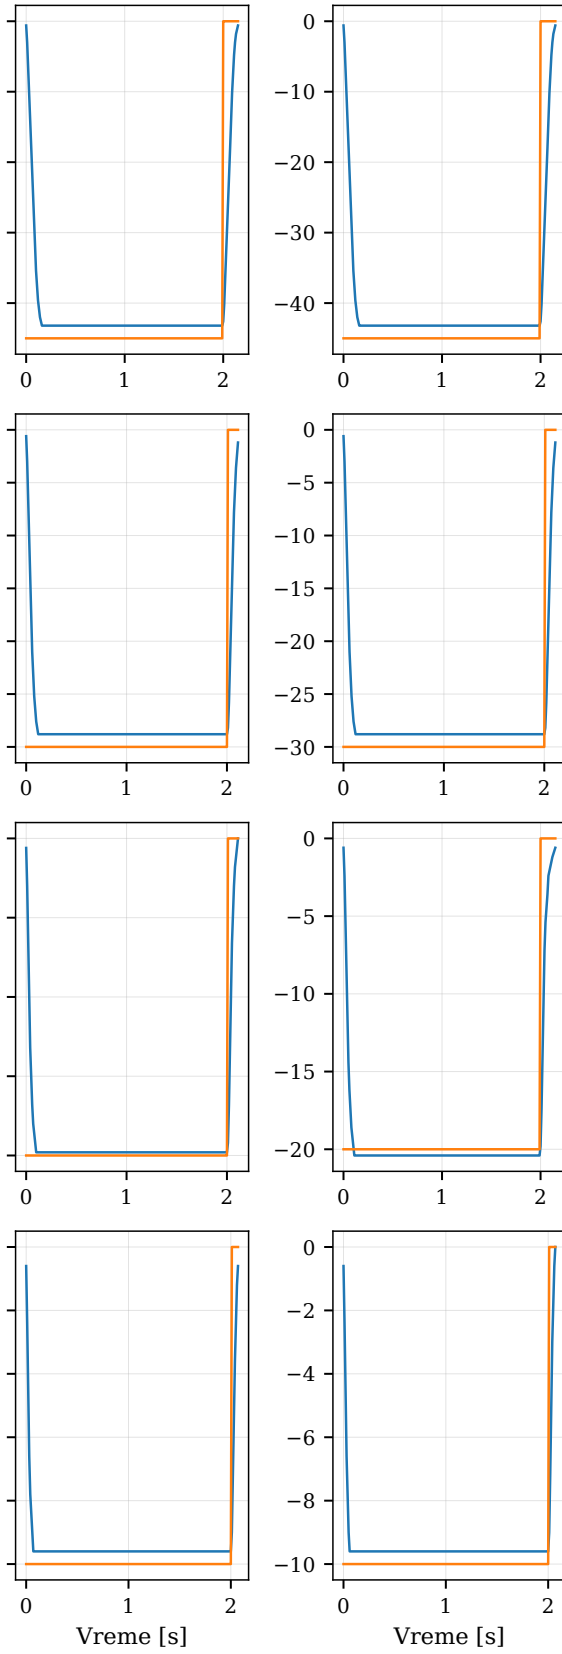
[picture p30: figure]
Vreme [s]
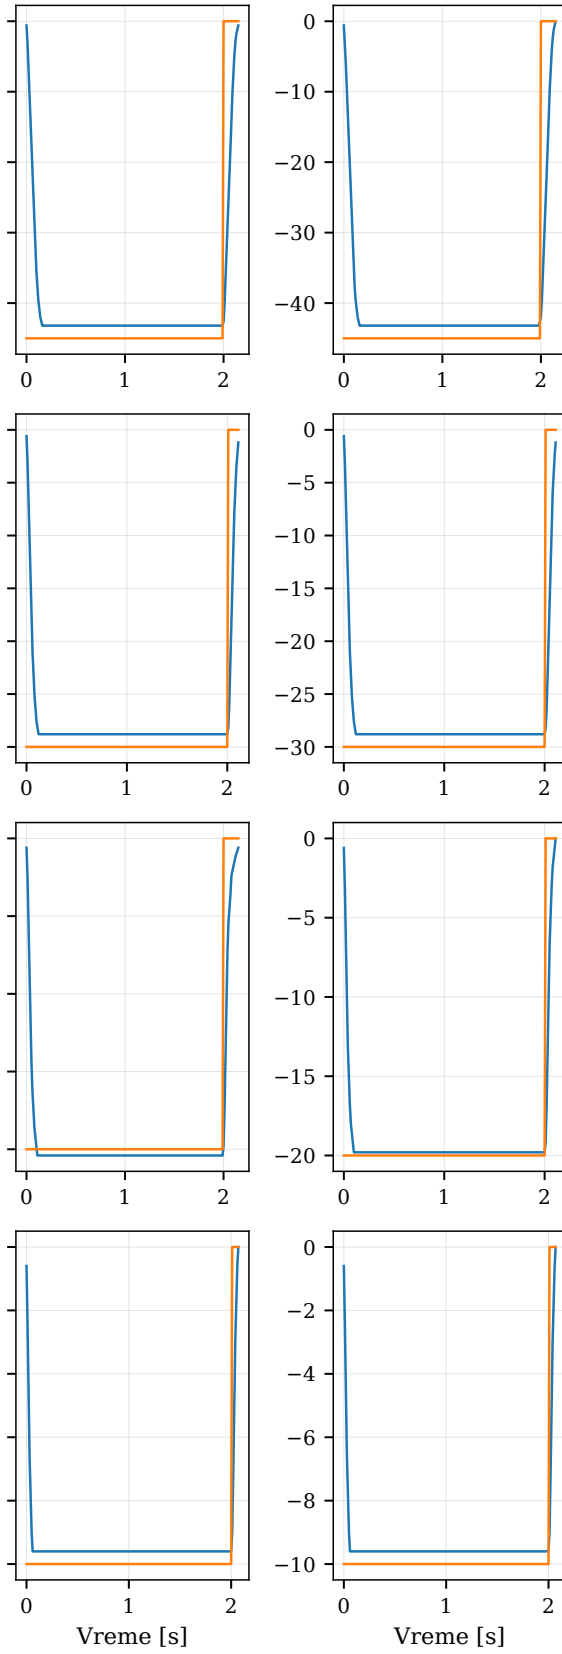
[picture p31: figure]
Vreme [s]
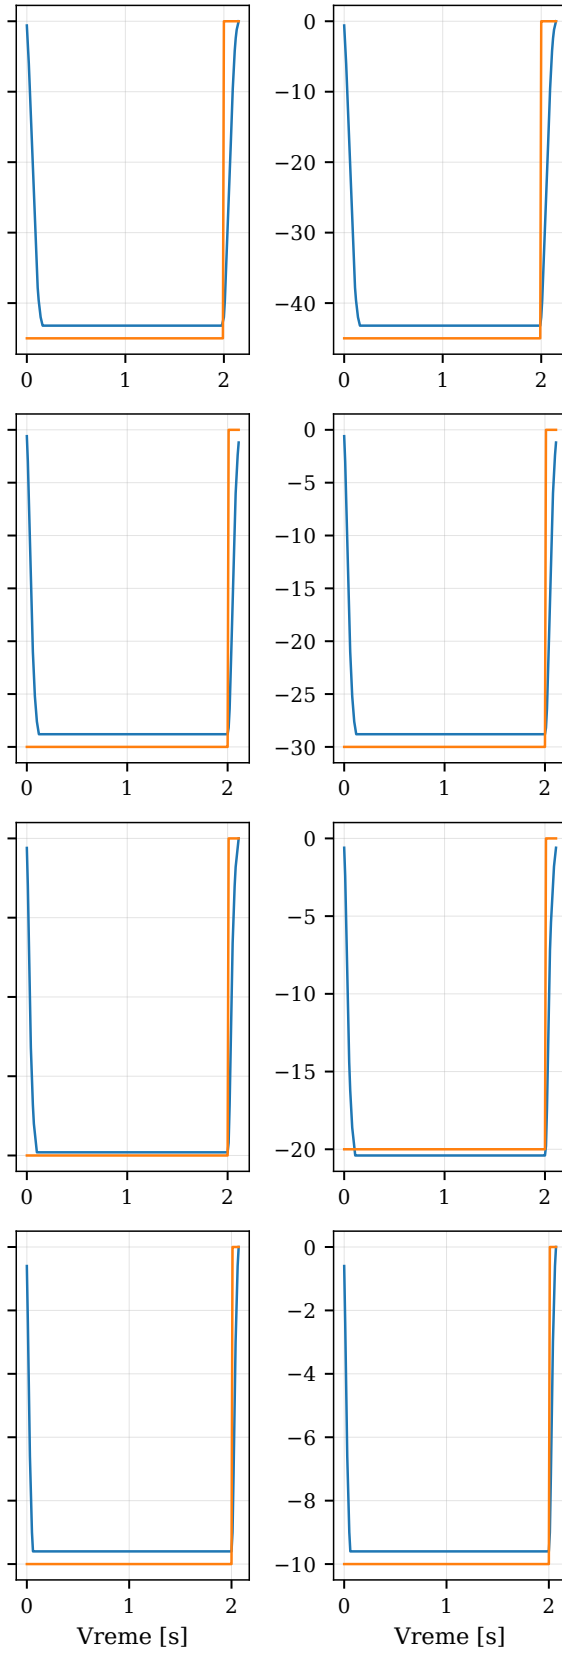
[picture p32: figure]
Vreme [s]
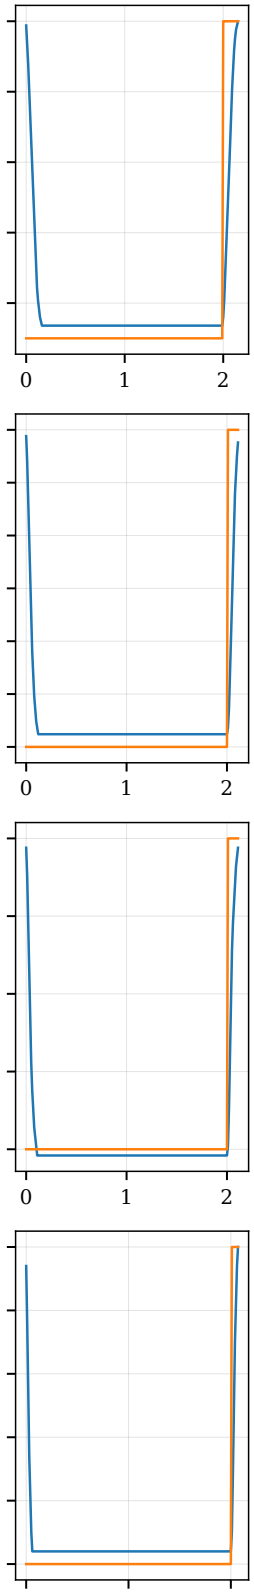
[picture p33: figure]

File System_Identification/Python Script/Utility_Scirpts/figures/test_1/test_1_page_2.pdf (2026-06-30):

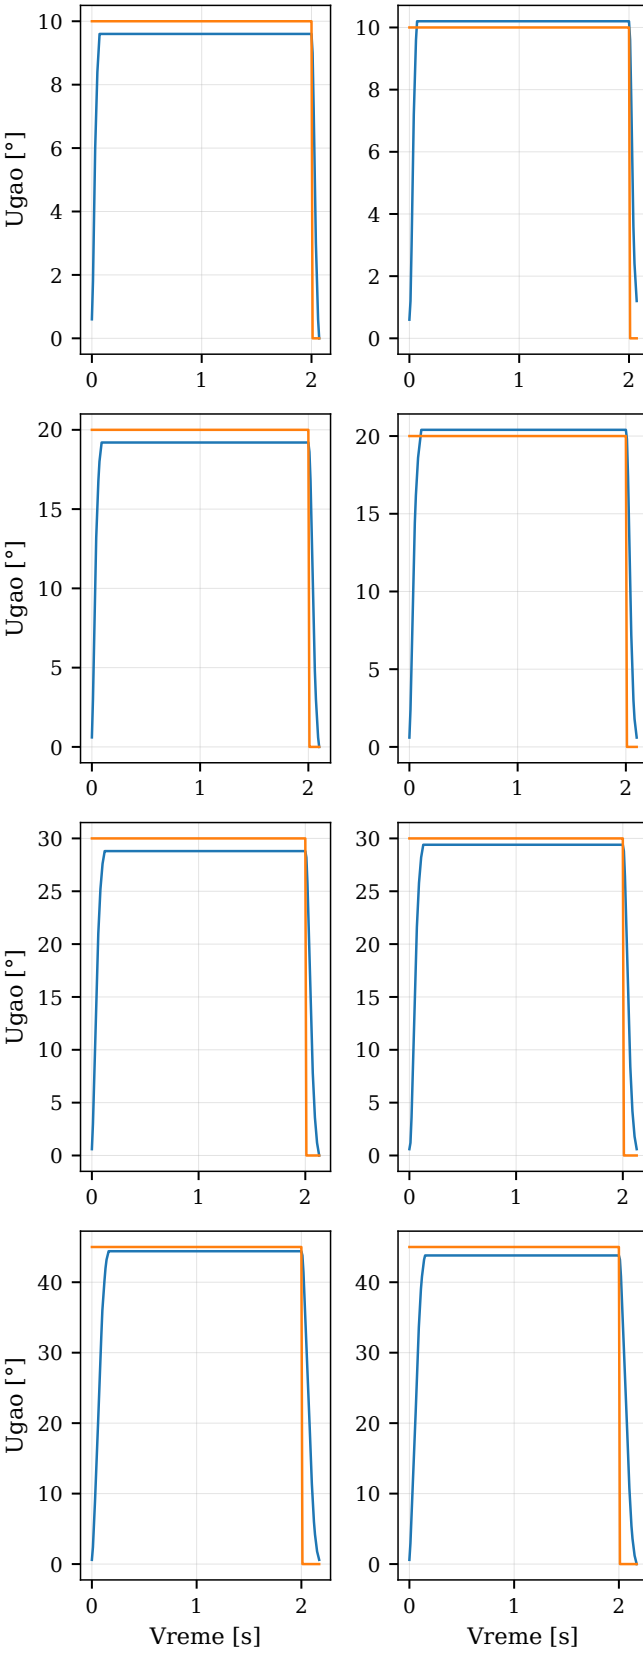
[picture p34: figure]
Ugao [°]; Vreme [s]
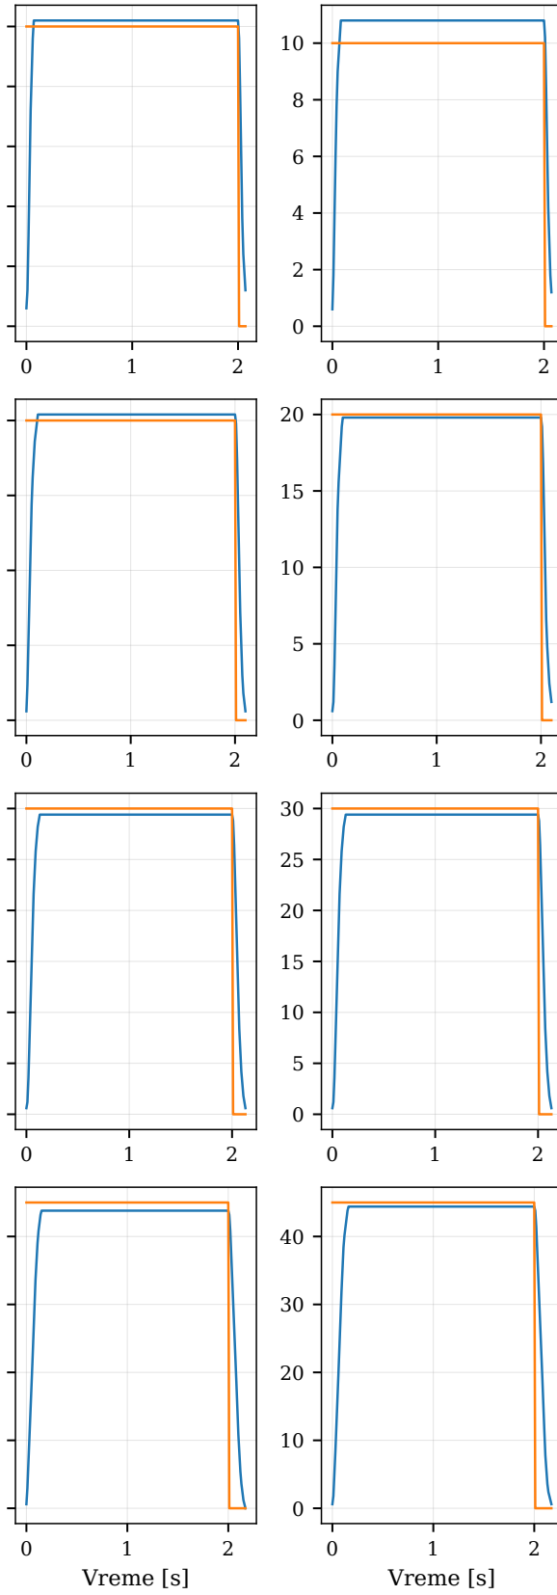
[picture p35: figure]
Vreme [s]
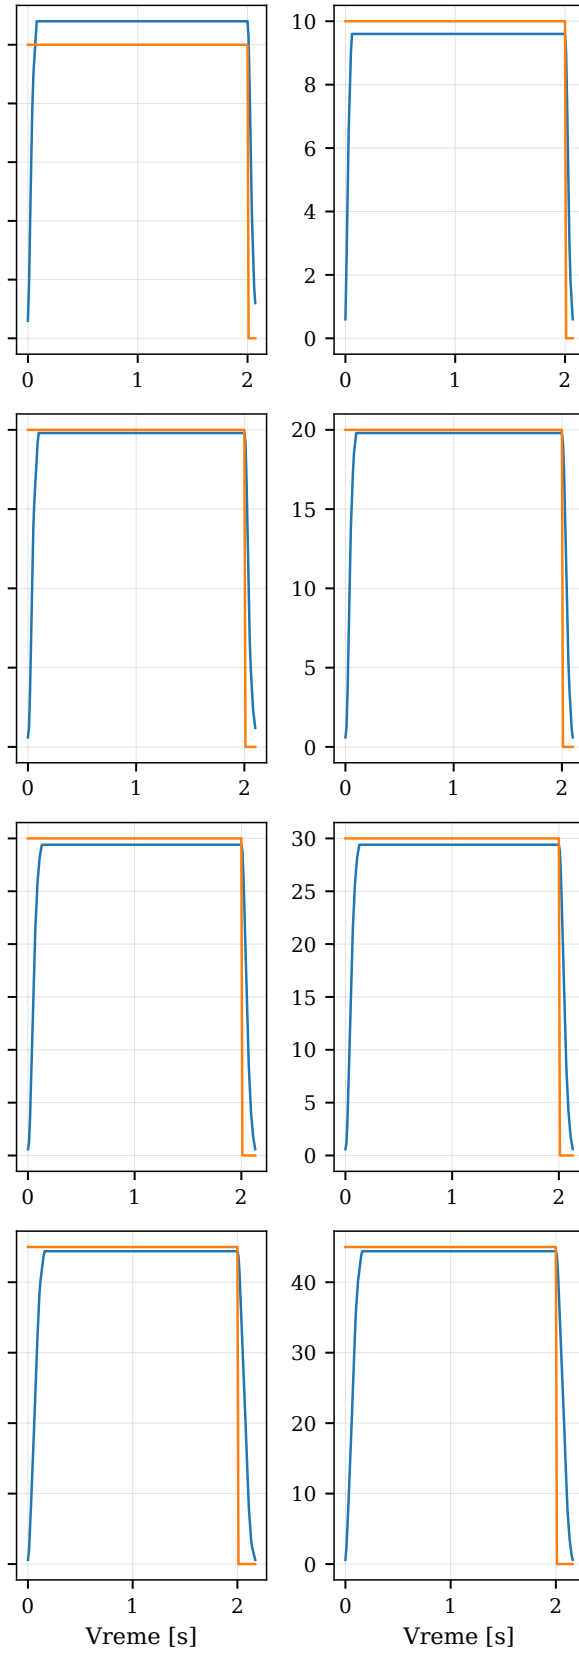
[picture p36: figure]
Vreme [s]
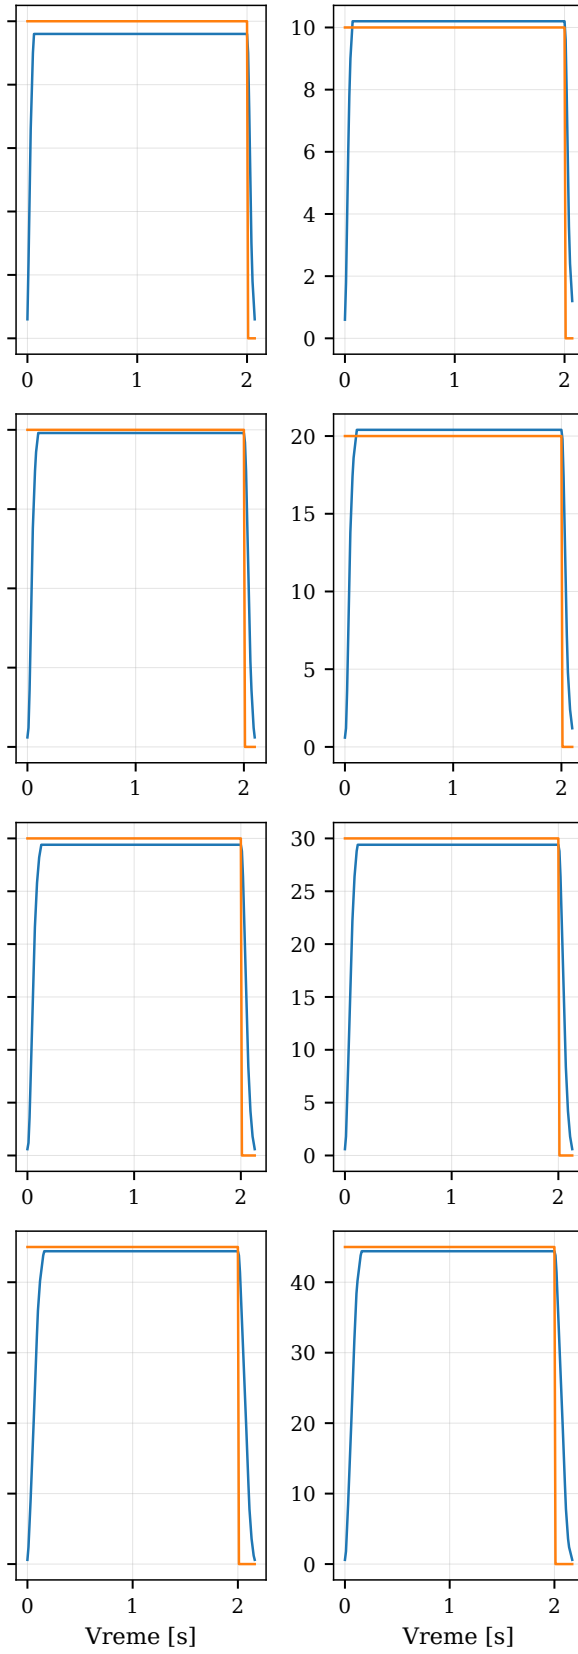
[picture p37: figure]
Vreme [s]
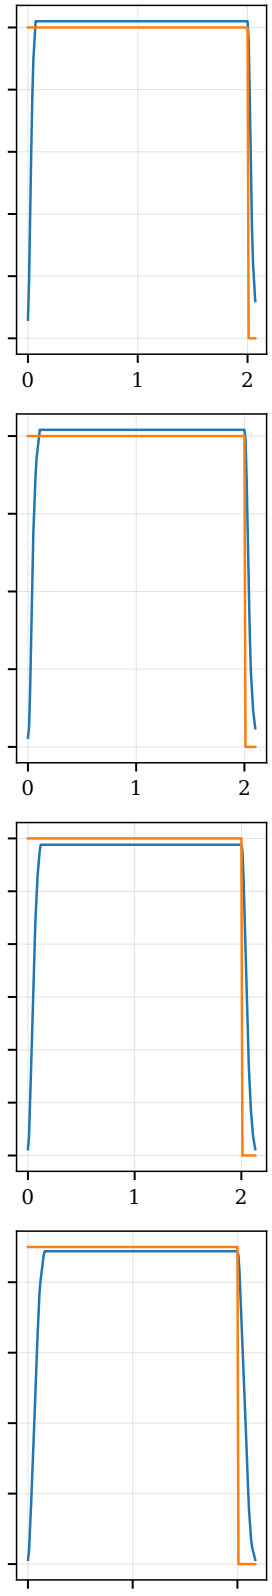
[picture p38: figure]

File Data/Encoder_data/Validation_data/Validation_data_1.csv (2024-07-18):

 | Angles | Time_s | PWM
0 | 0.6 | 0 | 24
1 | 1.8 | 0.01 | 24
2 | 3.6 | 0.02 | 24
3 | 6 | 0.03 | 24
4 | 7.2 | 0.04 | 24
5 | 9.6 | 0.05 | 24
6 | 11.4 | 0.06 | 24
7 | 13.8 | 0.07 | 24
8 | 15.6 | 0.08 | 24
9 | 18 | 0.09 | 24
10 | 19.2 | 0.1 | 24
11 | 20.4 | 0.11 | 24
12 | 21 | 0.12 | 24
13 | 21 | 0.13 | 24
14 | 21 | 0.14 | 24
15 | 21 | 0.15 | 24
16 | 21 | 0.16 | 24
17 | 21 | 0.17 | 24
18 | 21.6 | 0.18 | 24
19 | 21.6 | 0.19 | 24
20 | 21.6 | 0.2 | 24
21 | 21.6 | 0.21 | 24
22 | 21.6 | 0.22 | 24
23 | 21.6 | 0.23 | 24
24 | 21.6 | 0.24 | 24
25 | 21.6 | 0.25 | 24
26 | 21.6 | 0.26 | 24
27 | 21.6 | 0.27 | 24
28 | 21.6 | 0.28 | 24
29 | 21.6 | 0.29 | 24
30 | 21.6 | 0.3 | 24
31 | 21.6 | 0.31 | 24
32 | 21.6 | 0.32 | 24
33 | 21.6 | 0.33 | 24
34 | 21.6 | 0.34 | 24
35 | 21.6 | 0.35 | 24
36 | 21.6 | 0.36 | 24
37 | 21.6 | 0.37 | 24
38 | 21.6 | 0.38 | 24
39 | 21.6 | 0.39 | 24
40 | 21.6 | 0.4 | 24
41 | 21.6 | 0.41 | 24
42 | 21.6 | 0.42 | 24
43 | 21.6 | 0.43 | 24
44 | 21.6 | 0.44 | 24
45 | 21.6 | 0.45 | 24
46 | 21.6 | 0.46 | 24
47 | 21.6 | 0.47 | 24
48 | 21.6 | 0.48 | 24
49 | 21.6 | 0.49 | 24
50 | 21.6 | 0.5 | 24
51 | 21.6 | 0.51 | 24
52 | 21.6 | 0.52 | 24
53 | 21.6 | 0.53 | 24
54 | 21.6 | 0.54 | 24
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

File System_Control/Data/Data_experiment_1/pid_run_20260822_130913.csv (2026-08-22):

time_ms | distance_mm | beam_deg
9 | 378 | 45.0
68 | 380 | 45.0
126 | 386 | 45.0
186 | 376 | 11.46
245 | 381 | 45.0
303 | 381 | 45.0
363 | 374 | 45.0
422 | 359 | -45.0
481 | 372 | 45.0
540 | 360 | -35.38
599 | 350 | -19.33
658 | 364 | 45.0
717 | 343 | -45.0
777 | 345 | 45.0
835 | 346 | 45.0
894 | 335 | -45.0
954 | 342 | 45.0
1012 | 327 | -45.0
1071 | 329 | 45.0
1131 | 324 | 19.88
1189 | 310 | -45.0
1249 | 307 | 27.53
1308 | 299 | -45.0
1367 | 290 | -45.0
1426 | 279 | -45.0
1485 | 267 | -45.0
1545 | 260 | -45.0
1603 | 261 | 28.41
1662 | 256 | -45.0
1722 | 259 | 45.0
1780 | 254 | 45.0
1839 | 258 | 45.0
1899 | 266 | 45.0
1957 | 269 | 45.0
2017 | 272 | 45.0
2076 | 275 | 45.0
2135 | 267 | -45.0
2194 | 266 | 5.26
2253 | 262 | -41.53
2313 | 260 | -15.93
2371 | 257 | -33.52
2430 | 251 | -33.52
2490 | 254 | -33.52
2548 | 255 | -33.52
2607 | 253 | -33.52
2666 | 252 | -33.52
2725 | 258 | 45.0
2785 | 255 | 45.0
2843 | 265 | 45.0
2902 | 261 | -42.79
2962 | 256 | -45.0
3020 | 249 | -45.0
3080 | 248 | -45.0
3139 | 260 | 45.0
3197 | 262 | 42.41
3257 | 256 | -45.0
3316 | 267 | 45.0
3375 | 260 | -45.0
3434 | 259 | -3.17
3493 | 258 | -4.36
3552 | 248 | -4.36
3611 | 251 | -4.36
3670 | 250 | -4.36
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

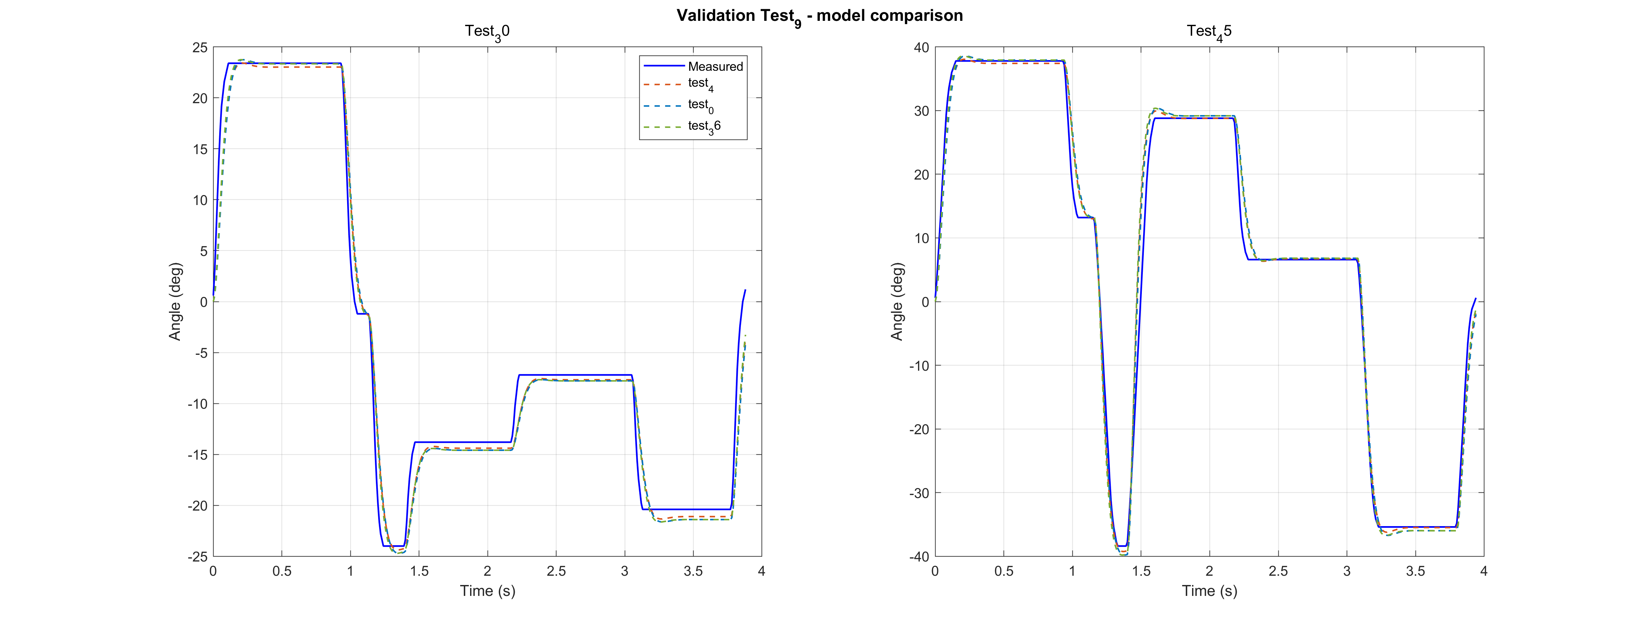
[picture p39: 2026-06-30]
System_Identification/Matlab_Scripts/Grey_Box/figures/grey_box_validation/compare/Test_9_model_compare.png

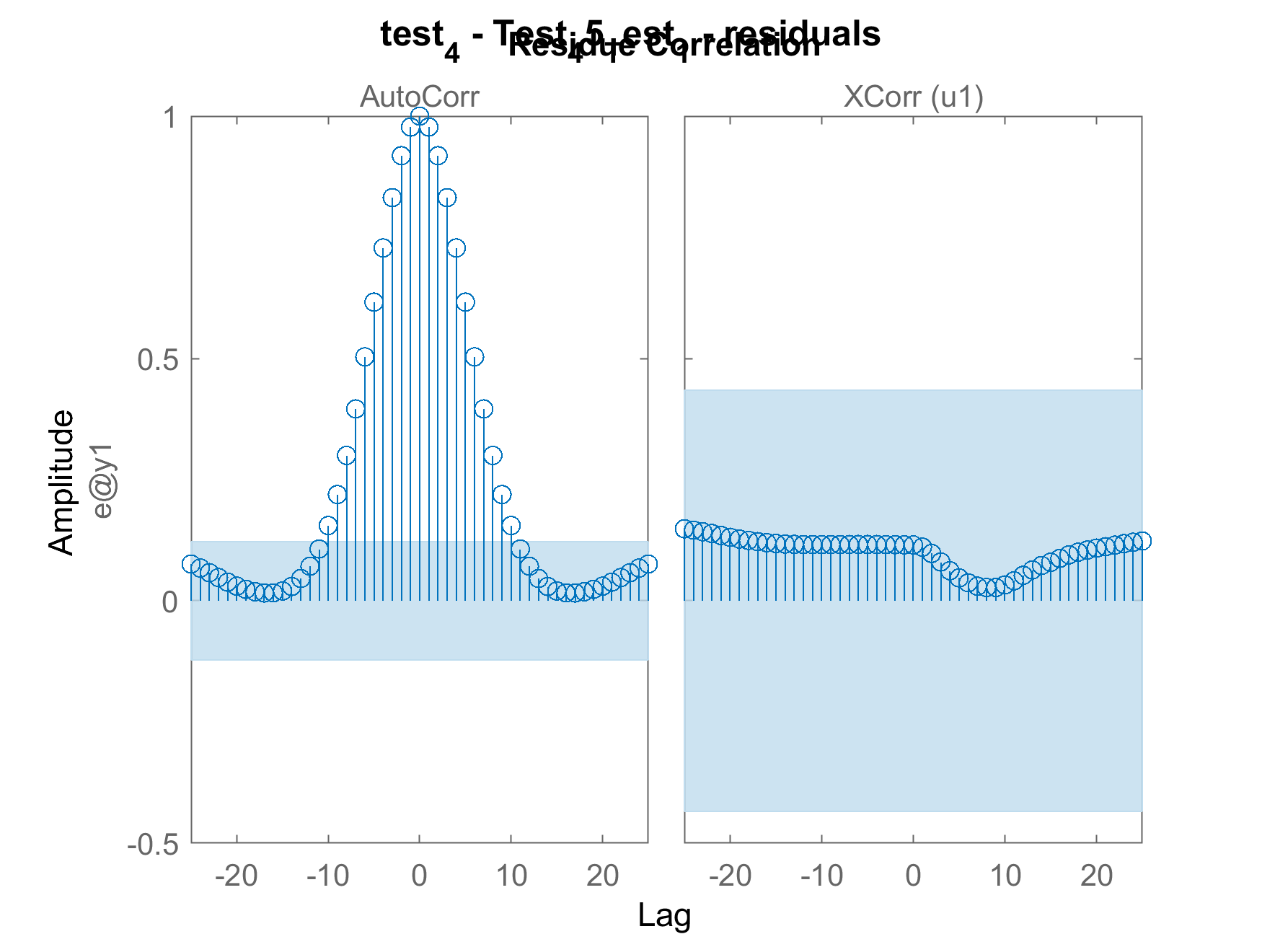
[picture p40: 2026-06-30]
System_Identification/Matlab_Scripts/Grey_Box/figures/grey_box_validation/residuals/test_4/test_4_Test_45_Test_1.png

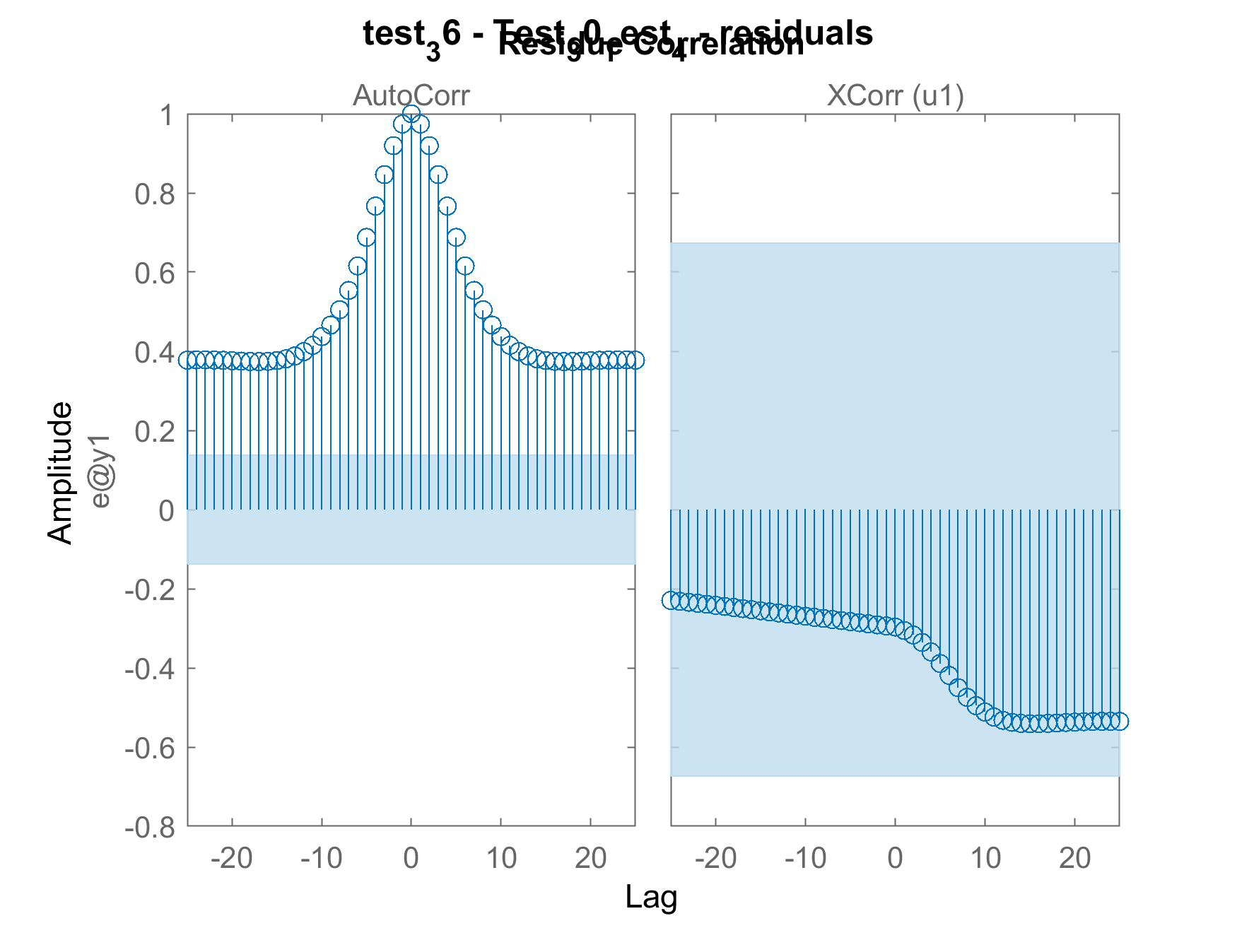
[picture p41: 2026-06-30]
System_Identification/Matlab_Scripts/Grey_Box/figures/grey_box_validation/residuals/test_36/test_36_Test_30_Test_4.png

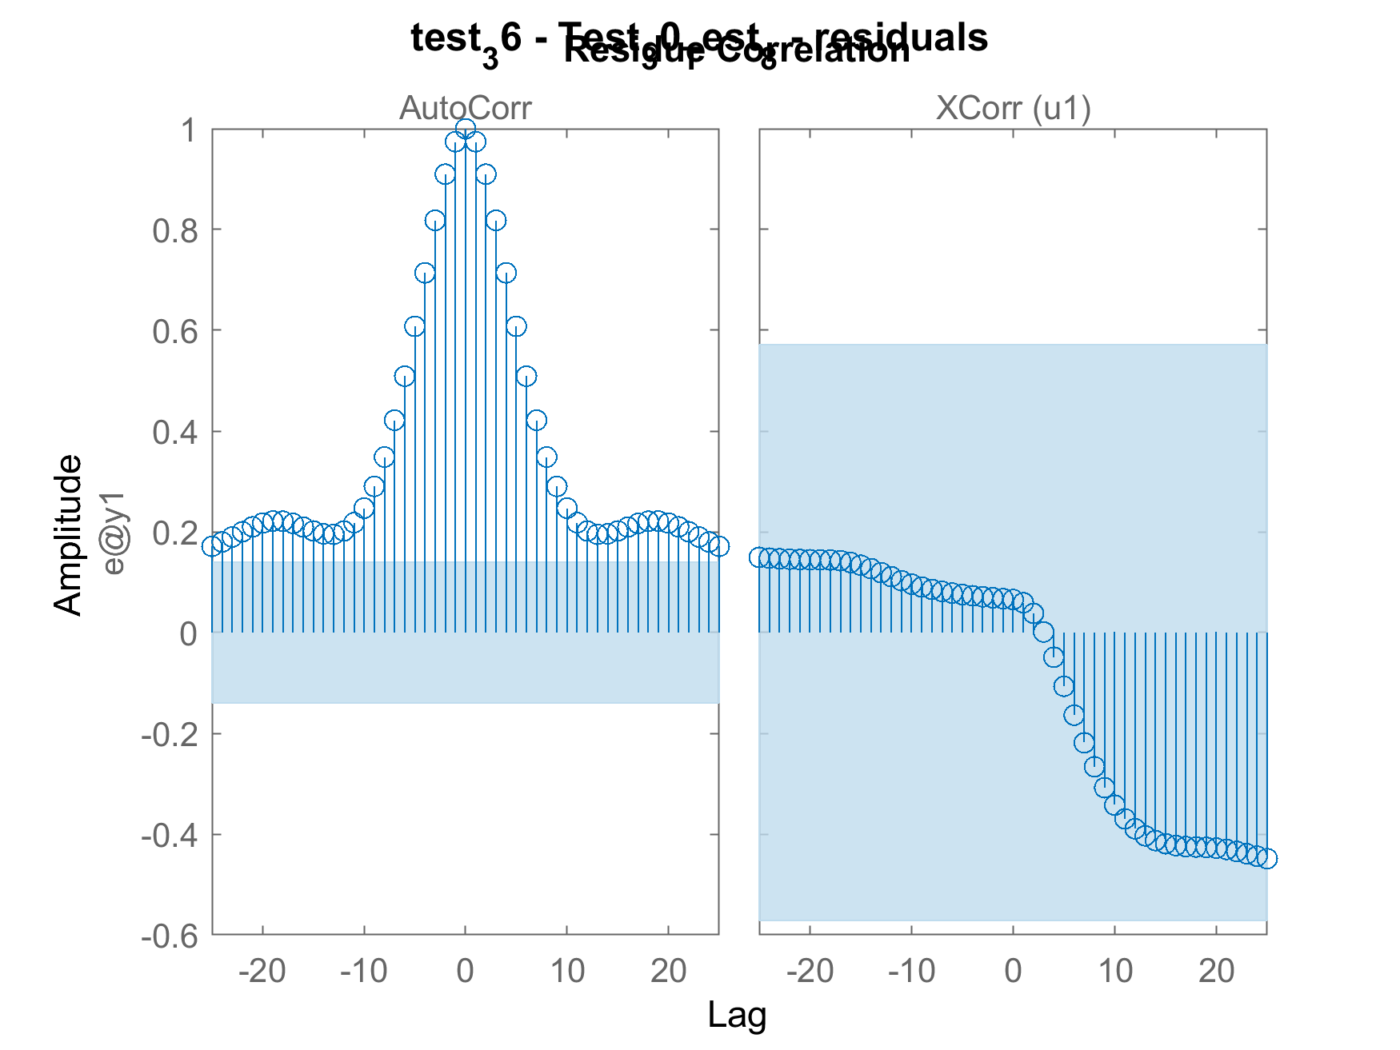
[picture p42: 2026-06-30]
System_Identification/Matlab_Scripts/Grey_Box/figures/grey_box_validation/residuals/test_36/test_36_Test_30_Test_8.png

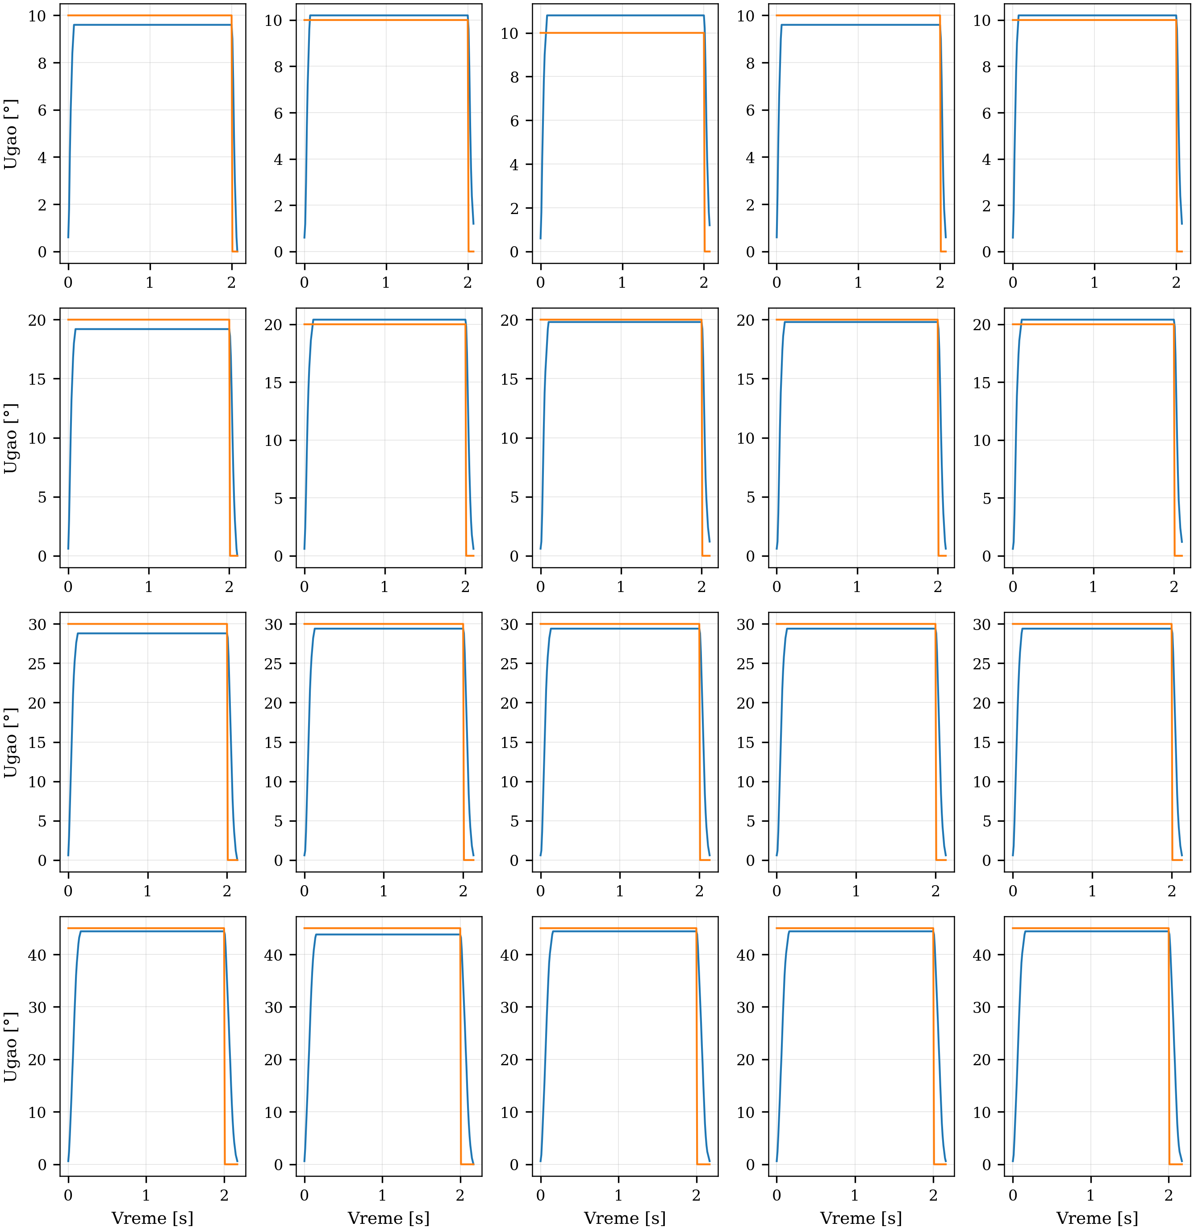
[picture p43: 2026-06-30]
System_Identification/Python Script/Utility_Scirpts/figures/test_1/test_1_page_2.png

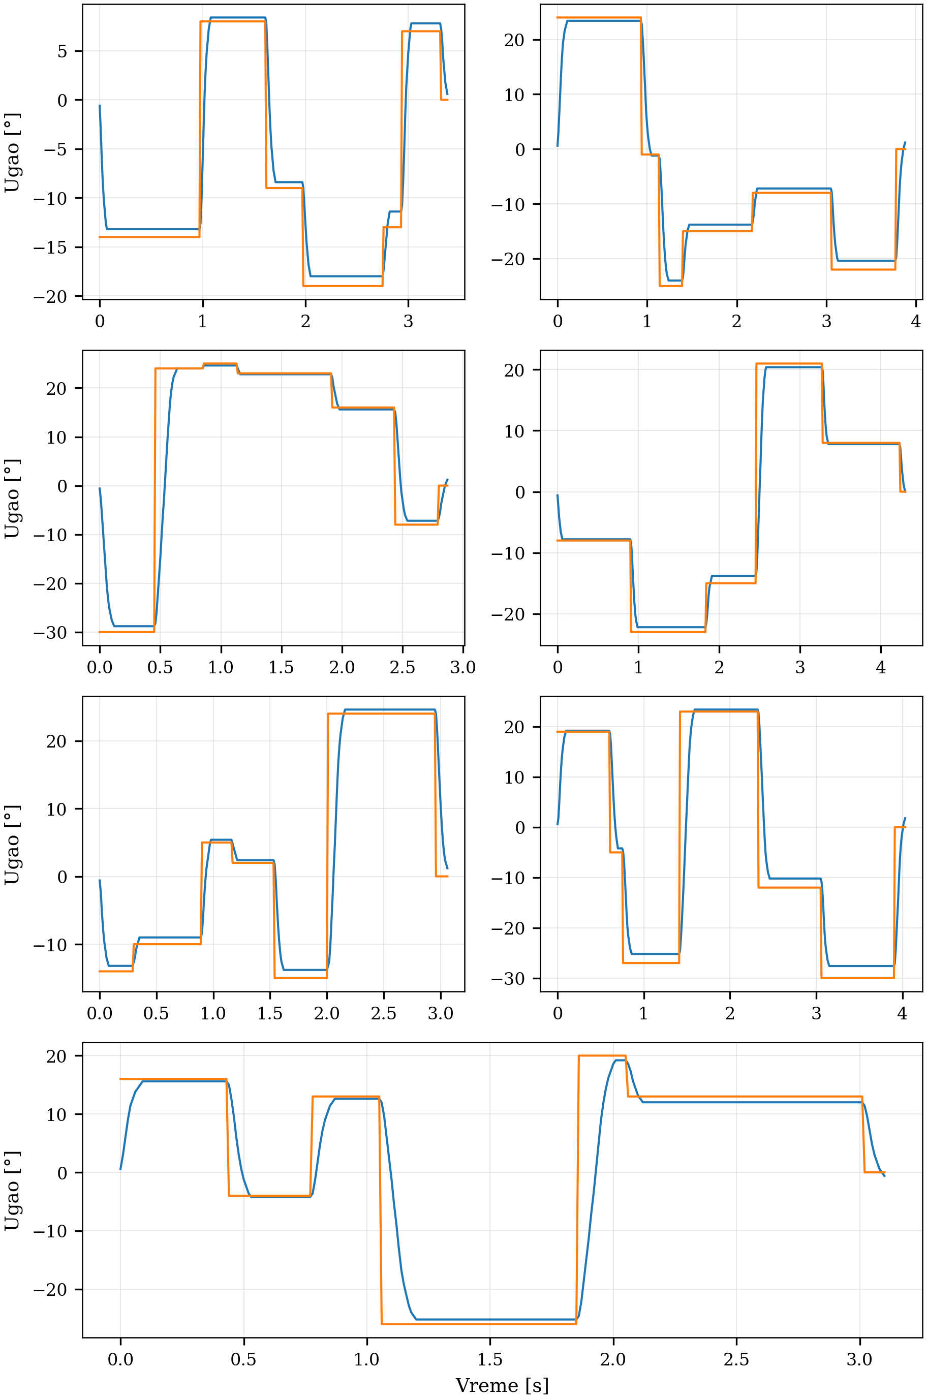
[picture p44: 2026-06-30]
System_Identification/Python Script/Utility_Scirpts/figures/test_2/Test_30_page_2.png

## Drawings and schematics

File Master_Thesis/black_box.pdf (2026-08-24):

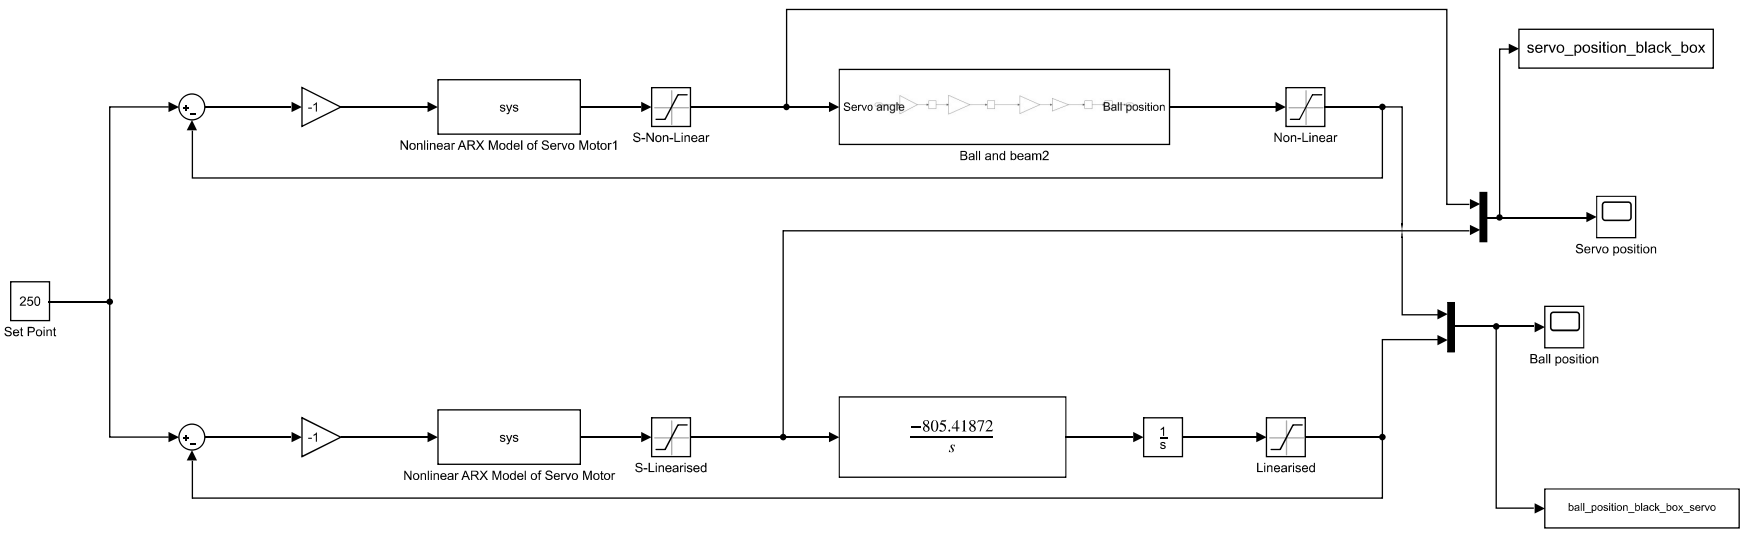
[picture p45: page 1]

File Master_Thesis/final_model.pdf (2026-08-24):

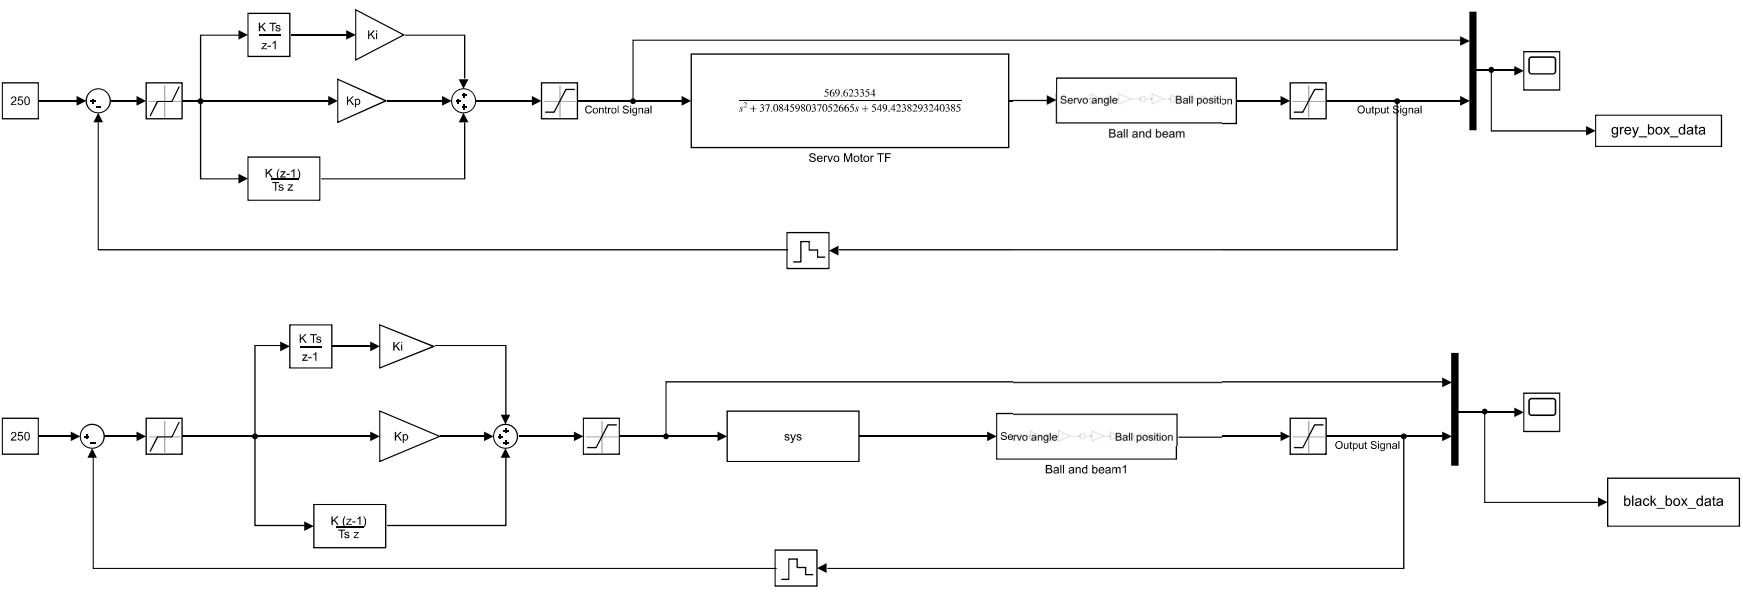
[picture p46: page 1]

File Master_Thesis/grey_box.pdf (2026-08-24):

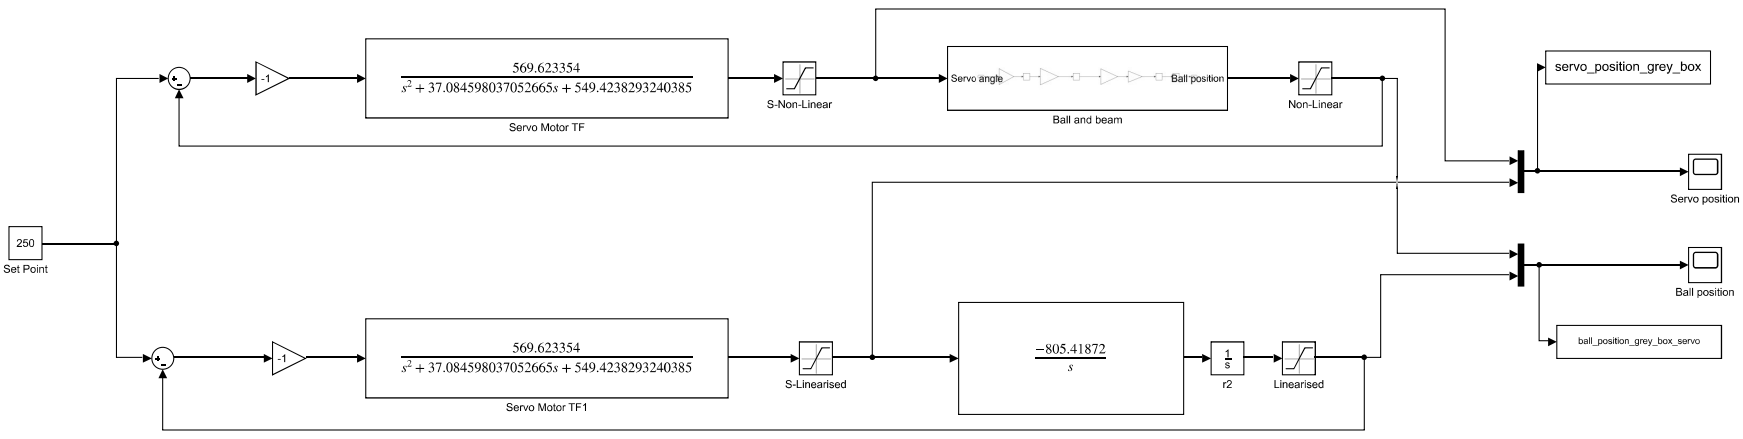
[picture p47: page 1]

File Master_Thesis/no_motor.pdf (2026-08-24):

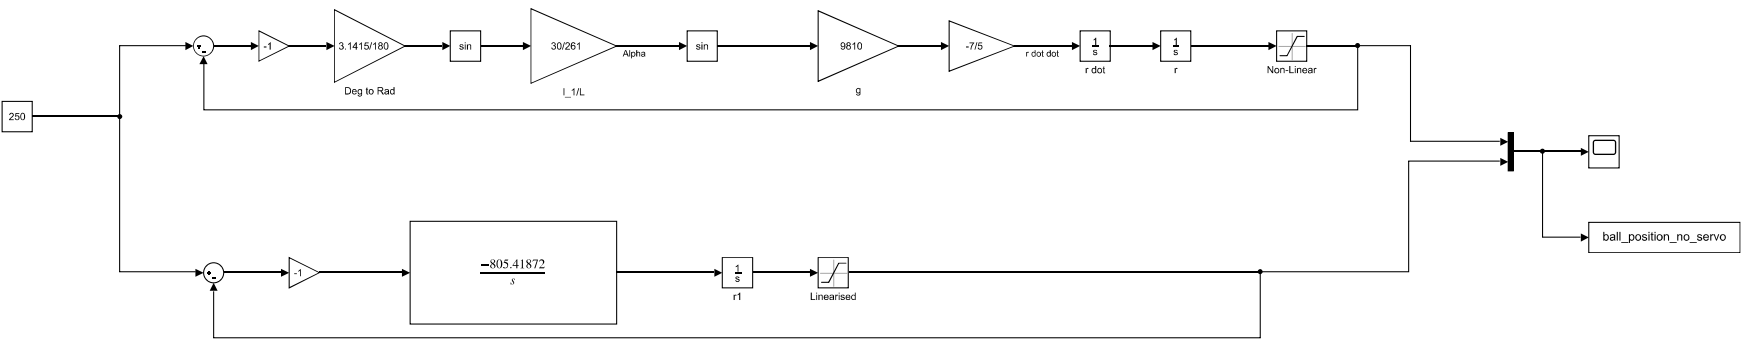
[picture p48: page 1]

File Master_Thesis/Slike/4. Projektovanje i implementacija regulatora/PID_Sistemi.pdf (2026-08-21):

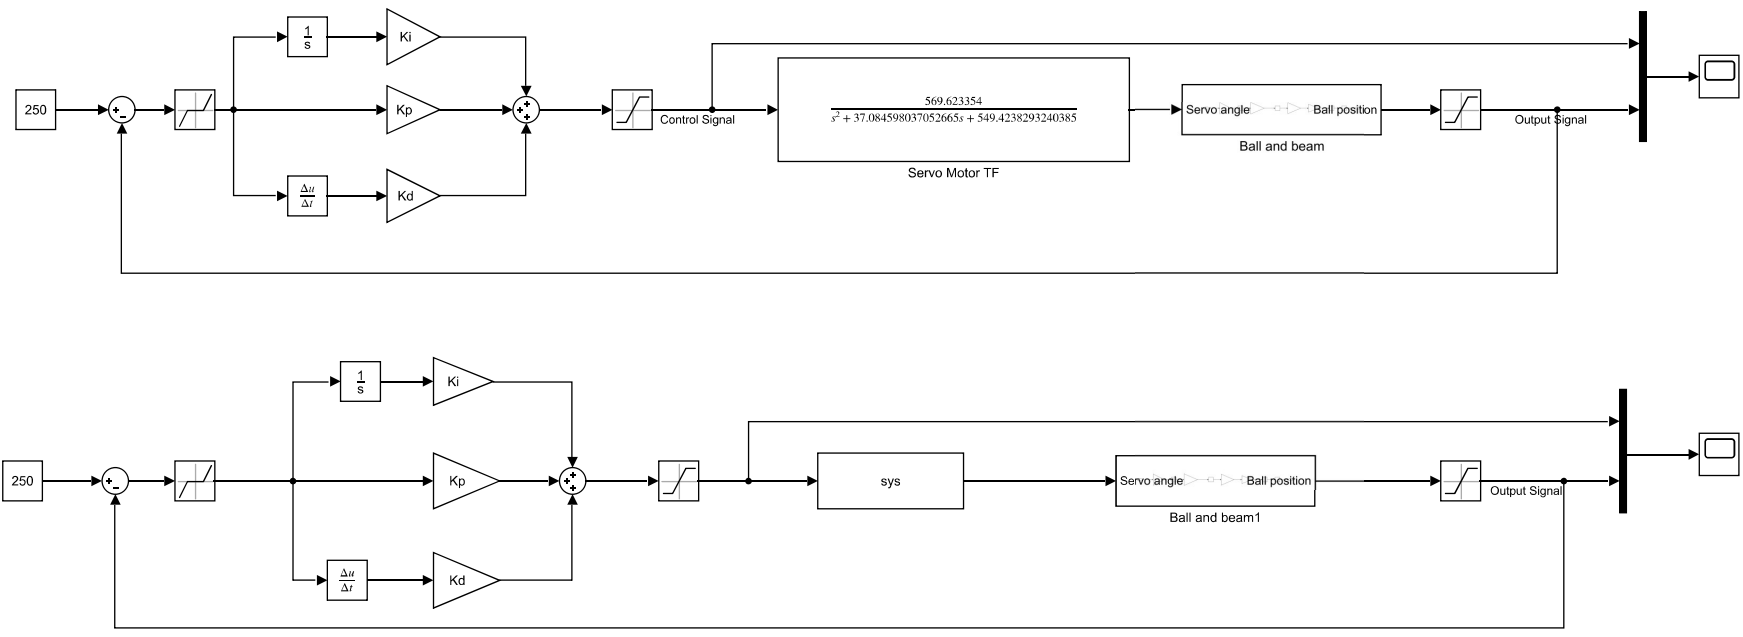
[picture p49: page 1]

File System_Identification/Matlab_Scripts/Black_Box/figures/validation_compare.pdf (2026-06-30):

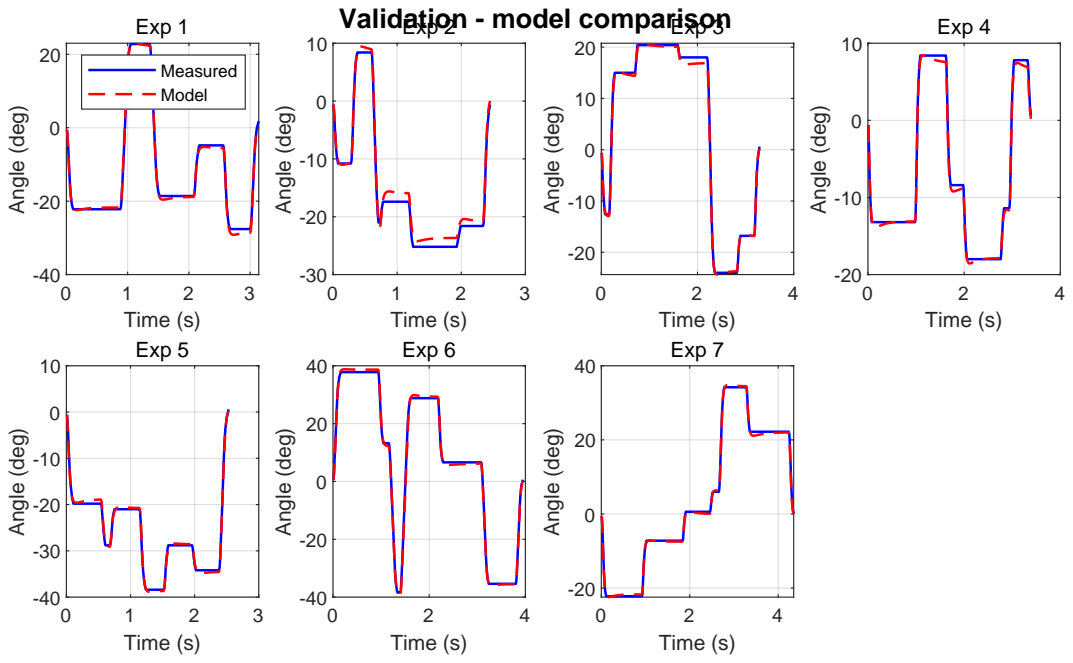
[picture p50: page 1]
Time (s); Angle (deg); Exp 1; Measured Model; Exp 3; Exp 4; Exp 5; Exp 6; Exp 7

Validation - model comparison
Exp 2

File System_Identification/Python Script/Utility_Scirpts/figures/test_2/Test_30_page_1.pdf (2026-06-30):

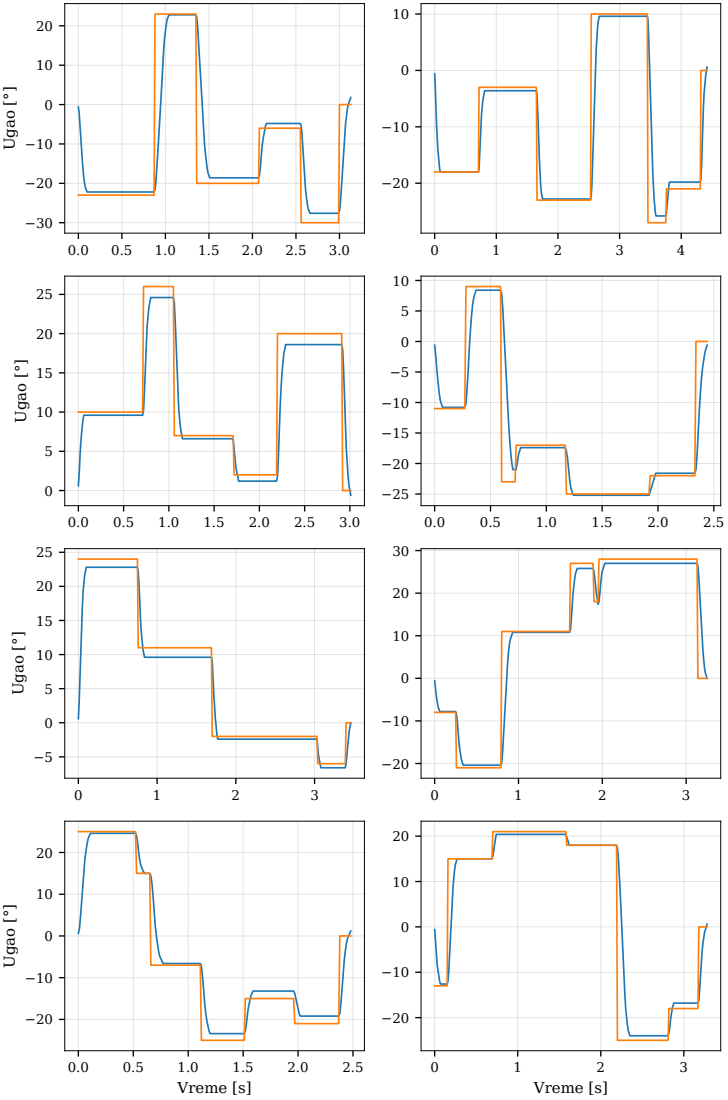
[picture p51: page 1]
Ugao [°]; Vreme [s]

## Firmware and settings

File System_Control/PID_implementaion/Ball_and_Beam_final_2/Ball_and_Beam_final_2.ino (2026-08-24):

#include <Servo.h>
#include "Adafruit_VL53L0X.h"

// ---------- Hardware ----------
const int SERVO_PIN = 5;
const int ZERO_PWM = map(0, -135, 135, 500, 2500);

const float BEAM_MIN = -45.0f;
const float BEAM_MAX =  45.0f;

Servo beamServo;
Adafruit_VL53L0X lox;

// ---------- Control ----------
const float SETPOINT_MM = 250.0f;
const float TOLERANCE_MM = 5.0f;
const unsigned long LOOP_MS = 50;

// First-order filter on the ball velocity only. The P and I terms still see the
// raw measurement, so this removes the noise the D term differentiates without
// delaying the rest of the loop.
const float D_TAU_S = 0.10f;

// Paste from MATLAB after tuning
float Kp = -1.2f;
float Ki = -0.01f;
float Kd = -0.7f;

bool running = false;
float distance_mm = 0.0f;
float beam_deg = 0.0f;
float integral = 0.0f;
float prev_error = 0.0f;
float d_filt = 0.0f;
bool sample_ready = false;
unsigned long t0_ms = 0;
unsigned long next_tick_ms = 0;

void setBeamAngle(float angle_deg) {
  float pwm_f = 500.0f + (angle_deg + 135.0f) * (2000.0f / 270.0f);
  int pwm = (int)lround(pwm_f);
  beamServo.writeMicroseconds(pwm);
}

void holdNeutral() {
  beam_deg = 0.0f;
  beamServo.writeMicroseconds(ZERO_PWM);
}

void readDistance() {
  if (!lox.isRangeComplete()) {
    return;
  }

  uint16_t raw = lox.readRange();
  if (raw != 65535) {
    distance_mm = (float)raw;
    sample_ready = true;
  }
}

float pidStep(float error) {
  if (fabs(error) <= TOLERANCE_MM) {
    integral = 0.0f;
    prev_error = 0.0f;
    d_filt = 0.0f;
    beam_deg = 0.0f;
    return beam_deg;
  }

  const float dt = LOOP_MS / 1000.0f;

  integral += error * dt;

  float d_raw = (error - prev_error) / dt;
  d_filt += (dt / (D_TAU_S + dt)) * (d_raw - d_filt);
  prev_error = error;

  beam_deg = constrain(Kp * error + Ki * integral + Kd * d_filt, BEAM_MIN, BEAM_MAX);
  return beam_deg;
}

void logData() {
  Serial.print(millis() - t0_ms);
  Serial.print(',');
  Serial.print((int)lround(distance_mm));
  Serial.print(',');
  Serial.println(beam_deg, 2);
}

void setup() {
  Serial.begin(115200);
  while (!Serial) {
    delay(1);
  }

  beamServo.attach(SERVO_PIN);
  holdNeutral();

  if (!lox.begin()) {
    Serial.println(F("VL53L0X init failed"));
    while (1) {
      delay(100);
    }
  }

  lox.startRangeContinuous();

  Serial.println(F("Ball and Beam v2 (D-filter)"));
  Serial.println(F("G = start, S = stop"));
  Serial.println(F("time_ms,distance_mm,beam_deg"));
}

void loop() {
  if (Serial.available()) {
    char cmd = Serial.read();
    while (Serial.available()) {
      Serial.read();
    }

    if (cmd == 'G' || cmd == 'g') {
      running = true;
      t0_ms = millis();
      next_tick_ms = t0_ms + LOOP_MS;
      integral = 0.0f;
      prev_error = 0.0f;
      d_filt = 0.0f;
      sample_ready = false;
      holdNeutral();
      Serial.println(F("RUN"));
    } else if (cmd == 'S' || cmd == 's') {
      running = false;
      holdNeutral();
      Serial.println(F("STOP"));
    }
  }

  // Poll the sensor as often as possible; the call returns immediately when no
  // new range is ready.
  readDistance();

  if (!running) {
    return;
  }

  if ((long)(millis() - next_tick_ms) < 0) {
    return;
  }
  next_tick_ms += LOOP_MS;
  if ((long)(millis() - next_tick_ms) > (long)LOOP_MS) {
    next_tick_ms = millis() + LOOP_MS;
  }

  // Without a fresh measurement the derivative would read zero and then double
  // on the next sample, so the command is held instead of recomputed.
  if (sample_ready) {
    sample_ready = false;
    float error = SETPOINT_MM - distance_mm;
    setBeamAngle(pidStep(error));
  }

  logData();
}

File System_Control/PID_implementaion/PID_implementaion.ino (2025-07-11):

#include <Servo.h>

// PID controller parameters
// float Kp = -7.169; // Proportional gain                 
// float Ki = -10.301; // Integral gain                    
// float Kd = -0.163; // Derivative gain                    
// float N = 163.68; // Filter coefficient for derivative  
 
float Kp = -2.49;
float Ki = -0.18;
float Kd = -5.1;
float N = 1178.01;

float dt = 0.2; // Time step (10 ms)
float integral = 0; // Integral sum
float prev_error = 0; // Previous error for derivative calculation
float prev_derivative = 0; // For filtering the derivative

float control_output = 0; // PID control output

// Setpoint and feedback
int setpoint = 25; // Desired distance in cm
float feedback = 0; // Measured distance from ultrasonic sensor
 
int angle_0 = 95;
bool systemActive = false;
Servo myServo;

void setup() {
  Serial.begin(115200); // Set baud rate to 115200 for faster data transmission

  // Initialize servo motor
  myServo.attach(9, 580, 2420);

  // Initialize ultrasonic sensor pins
  pinMode(5, OUTPUT);  // Triger Pin  zelena/plava
  digitalWrite(5,LOW);
  pinMode(6, INPUT);  // Eho pin zuta

  // Set initial servo position to neutral (90 degrees or center of the range)
  myServo.write(angle_0);
  feedback = 0;
  prev_derivative = 0;
  prev_error = 0;
}

void loop() {
  if (Serial.available() > 0) {
    char command = Serial.read(); // Read the incoming byte

    if (command == 'S') {
      systemActive = false; // Stop the system
      myServo.write(angle_0); // Optionally, set servo to neutral position
      Serial.println("System stopped");
    }
    else if (command == 'G') {
      systemActive = true; // Start the system
      Serial.println("System running");
    }
    else if (command == 'R'){
      systemActive = false;
      float distance = getUltrasonicDistanceBlocking();
      Serial.println(distance);
    }
  }

  if (systemActive) {
    // Measure distance using blocking ultrasonic sensor
    float distance = getUltrasonicDistanceBlocking();
    
    // If a valid distance is returned, update feedback
    if (distance != -1) {
      feedback = distance;
    }

    // Compute error
    float error = setpoint - feedback;

    // Proportional term
    float P = Kp * error;

    // Integral term
    integral += error * dt;
    float I = Ki * integral;

    // Derivative term with filter
    float derivative = (error - prev_error) / dt;
    float filtered_derivative = (N * derivative + prev_derivative) / (1 + N * dt);
    float D = Kd * filtered_derivative;
    // float D = Kd * derivative;
    // PID output
    control_output = P + I + D;

    // Constrain output to the range of -30 to 30 degrees
    control_output = constrain(control_output, -30.0, 30.0);
    control_output += angle_0;

    // Map the control output to the servo's PWM range
    int pwmValue = map(control_output, 0, 180, 580, 2420);

    // Send the PWM signal to the servo motor
    myServo.writeMicroseconds(pwmValue);
    // delay(250);

    // Update previous values for the next loop
    prev_error = error;
    // prev_derivative = filtered_derivative;

    // Send only the distance value over serial communication
    // unsigned long currentTime = millis(); // Get the elapsed time in milliseconds
    // Serial.println(currentTime);
    Serial.println(feedback);
  }

  // Wait for the next loop iteration (10 ms)
  delay(dt * 1000);
}

// Function for blocking ultrasonic distance measurement
float getUltrasonicDistanceBlocking() {
  // Send a 10µs pulse to trigger the sensor
  digitalWrite(5, LOW);
  delayMicroseconds(2);
  digitalWrite(5, HIGH);
  delayMicroseconds(10);
  digitalWrite(5, LOW);

  // Measure pulse duration
  long duration = pulseIn(6, HIGH);

  Serial.println(duration);
  // Calculate distance in centimeters
  float distance = (duration / 2.0) * 0.0344 + 3; // Speed of sound is 0.0344 cm/µs; radius of ball ball 3cm 

  // Return distance
  return distance;
}

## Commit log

2023-08-18 Pocetak, skripta za zadavanje komandi servo motoru je gotova
2023-08-18 Virtual ENV --> Set Up, requirments.txt --> added, python script for serial communication started
    [pyvenv.cfg]
2023-09-26 Skripta za enkoder sredjena, skripta za servo sredjenja, pobrisane nepotrebne stvari i ubacen gitignore
2024-01-13 Enviroment set up, Python Script for data colecting and Servo Script
2024-01-13 Removing chashed folder
    [pyvenv.cfg]
2024-01-20 RPi - space added, Python script - Script for data collection finished, Servo_script - Some minor chages regarding logic
2024-01-20 RPi rename of folder; Servo_Script - pwm signal fix; Python Scripts - Data_processing script init code
    [Encoder_script_01.py, Encoder_script_02.py, Servo_script.ino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]
2024-04-20 Obrada prostih podataka zavrsena
    [Test_0.csv, Test_1.csv, Test_10.csv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]
2024-06-29 Nova skript za sredjivanje podataka, novi podaci, Grey_box model za estimaciju i Black box modeli za estimaciju
    [Test_0.csv, Test_1.csv, Test_10.csv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]
2024-07-01 Data_Proccessing_3 - Processing data from 3rd/radnom test
    [Test_0.csv, Test_1.csv, Test_2.csv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]
2024-07-01 New data generated + some little changes
    [Test_0.csv, Test_1.csv, Test_2.csv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]
2024-07-06 New data for test_3 and few addaptions in scripts
    [Test_0.csv, Test_1.csv, Test_2.csv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]
2024-07-06 Neke izmene, ne znam koliko su dobre
    [Test_0.csv, Test_1.csv, Test_2.csv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]
2024-07-07 Encoder script improved + not important changes
2024-07-07 Removing data with issue
    [Test_0.csv, Test_1.csv, Test_10.csv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]
2024-07-07 New semi processed data
    [Test_0.csv, Test_1.csv, Test_10.csv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]
2024-07-07 Data preprocessing finished
    [Test_0.csv, Test_1.csv, Test_2.csv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]
2024-07-15 Simple data processed
    [Test_0.csv, Test_1.csv, Test_10.csv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]
2024-07-15 Complicated data processe in progress
    [Test_1.csv, Test_2.csv, Test_3.csv]
2024-07-16 Data from test 3 processed + script
    [Test_0.csv, Test_1.csv, Test_2.csv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]
2024-07-16 Manual correction done
    [Test_0.csv, Test_1.csv, Test_2.csv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]
2024-07-16 Data for validation + Skript for data for validation + Renamed other 2 scripts for data processing
    [Validation_data_1.csv, Validation_data_2.csv]
2024-07-22 Grey Box done - to be improved
    [Grey_Box.csv]
2024-07-22 Validation data for Grey Method REDY
    [Val_Data_0.csv, Val_Data_1.csv, Val_Data_2.csv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]
2024-07-22 Grey box done - maybe one more improvment is left
    [Grey_Box.csv, Val_Data_0.csv]
2024-07-23 Grey Box Estimation is Done :D
    [GreyBoxFinal.csv, Grey_Box.csv]
2024-07-23 PID Estimation - beggining
2024-08-13 Master rad - Ultrasonicni senzor done
2024-08-17 Uklanjanje nepotrebne kolone, reorganizacija i pisanje koda za grey_box estimaciju
    [Test_0.csv, Test_1.csv, Test_10.csv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]
2024-08-24 CAD Model sistema, Grey box matlab skripte, Master rad dokument se menjao i jos mnogo toga
    [Balanser Ping Pong Lopte.CATProduct, Baza.CATPart, CrystalOscillator.CATPart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]
2024-08-25 First step of reorganisation
    [Balanser Ping Pong Lopte.CATProduct, Baza.CATPart, CrystalOscillator.CATPart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]
2024-09-01 Test bench CAD model added
    [Baza.CATPart, ISO_7046-2_M4x16-H2_STEEL_GRADE_A_COUNTERSUNK_FLAT_HEAD_SCREW.CATPart, Nosac Rotacionog Enkodera.CATPart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]
2024-09-07 Master rad doc update, script for ploting test 3 data and small changes
    [Val_Data_6.csv]
2024-09-09 System identification - grey box method is done
    [Est_data.csv, Est_data_1.csv, Model_1.csv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]
2024-09-09 Master rad doc update and removal of files that, in the end, don't mathers
    [Est_data_1.csv, GreyBoxFinal.csv, Grey_Box.csv]
2024-09-11 Data for Black Box estimation prepared
    [TestData.csv, Val_Data_0.csv, Val_Data_2.csv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]
2024-09-11 Black box estimation done
    [TestData.csv, ValidationData.csv]
2024-09-12 Black box done :D
    [TestData.csv, ValidationData.csv]
2024-09-15 Master doc update + PID regulator
2026-06-19 new data
    [Val_Data_0.csv, Val_Data_1.csv, Val_Data_2.csv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]
2026-06-19 Model upgrade
    [Balanser Ping Pong Lopte.CATProduct, Baza.CATPart, CrystalOscillator.CATPart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]
2026-06-26 Black box done
    [TestData.csv, ValidationData.csv]
2026-06-30 CAD model update
    [Balanser Ping Pong Lopte.CATProduct, Baza.CATPart, CrystalOscillator.CATPart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]
2026-06-30 System identification done
    [Model.csv, Model_1.csv, Model_2.csv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]
